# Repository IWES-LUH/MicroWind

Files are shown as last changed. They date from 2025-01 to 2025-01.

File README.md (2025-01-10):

# MicroWind
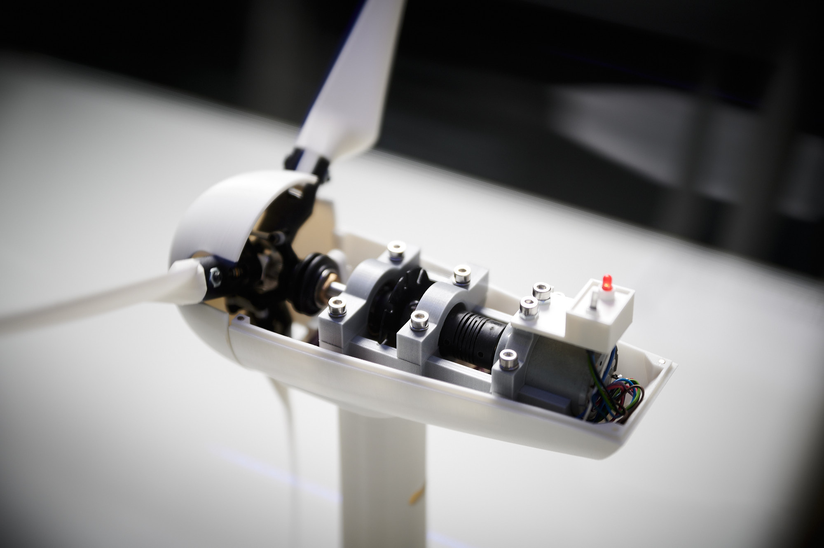
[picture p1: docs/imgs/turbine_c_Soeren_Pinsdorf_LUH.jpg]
Turbine image

*(c) Soeren Pinsdorf / LUH*

MicroWind is an easy to build, 3D-printed miniature wind turbine model 
equipped with various functionalities and sensors. 
The project also features a graphical interface for turbine and wind tunnel control 
and real-time measurement data plots. Its aim is an educational purpose: 
to convey the behavior of a wind turbine in different operation conditions.  
**It is not suited for electricity generation.**  
The repository contains the stl files for 3D printing, the source code for the arduino microcontroller, 
the source code for the graphical interface written in python and tkinter and the documentation.

## Features
* Wind turbine with rotor diameter of 320mm.
* Rated wind speed between 2.5 and 3 m/s.
* Variable blade pitch.
* Variable torque (with limitations).
* Rotation speed measurement.
* Power measurement.
* Thrust force measurement.
* Wind speed measurement with thermal anemometer.
* Bearing friction compensation.
* Compact and appealing wind tunnel design.
* Wind tunnel speeds up to 6 m/s.
* Easy to use user interface for control and measurement display.
* Python template script for easy programming pitch and torque controller (e.g. PID).
* Arcade style game where you have to set pitch in varying wind conditions

## Requirements
The software will be provided as source code to run in a Python interpreter. 
You will need a Python installation and some additional packages to run the software.
Check [requirements.txt](interface/requirements.txt) for the additional packages and 
the installation guideline in the [documentation.md](docs/documentation.md).

The gui works well on Windows systems and is designed and tested on Windows. 
It also works on linux systems with a few minor graphical issues which may be fixed in the future.
The additional package python3-tk is required on debian and python3-tkinter on fedora systems. 
For the arcade game to work properly, a 1920x1200 screen is required. 
For now, the arcade game graphics are not scalable. 

## Required skills
The project is designed for an easy build. However, depending on where and when you are building the turbine, 
some parts may not be available and some alterations must be made. 
Therefore, the project requires some skills:
* Soldering, and basic understanding of electronic circuit design.
* Precise 3D-printing. FDM is fine, but you will need a nozzle size of 0.25 for some parts.
* Postprocessing 3D-printed parts, drilling, inserting threaded inserts.
* Arduino programming, if one of the sensors has to be replaced with a different brand.
* Python programing if you want to tailor the GUI to your needs.
* General troubleshooting ability and patience. 
Even a good documentation is never perfect.  
And this one is not a step by step manual (yet). You may need to dig a little to get it working.  

If you find yourself comfortable tackling the aforementioned requirements then we wish you a **happy build!** 
If you run into trouble don't hesitate to ask.

## Contribution
We decided to publish the project on GitHub, so it is easy for you to contribute. 
Whether you are a software developer willing to improve the code, 
or you stumbled across some shortcomings in the documentation while building, 
we kindly ask you to contribute your upgrades to the project. 
The project is mostly created by mechanical / wind energy engineers, who are not professionals in all fields. 
We believe that there are still many improvements to make. See [contribution.md](contribution.md) for open issues.

## Acknowledgements
The initial MicroWind project was funded for the improvement of study
conditions by the Leibniz University Hannover.

## License
The software is licensed under GPLv3.  
The 3D-parts for printing and the documentation is licensed under CC-BY 4.0.
See [LICENSE.md](LICENSE.md) for more information about GPLv3 and CC-BY 4.0.  

The theme for the GUI is licensed under the MIT license
See [LICENSE-Third-Party.md](LICENSE-Third-Party.md) for more information

## Impressions
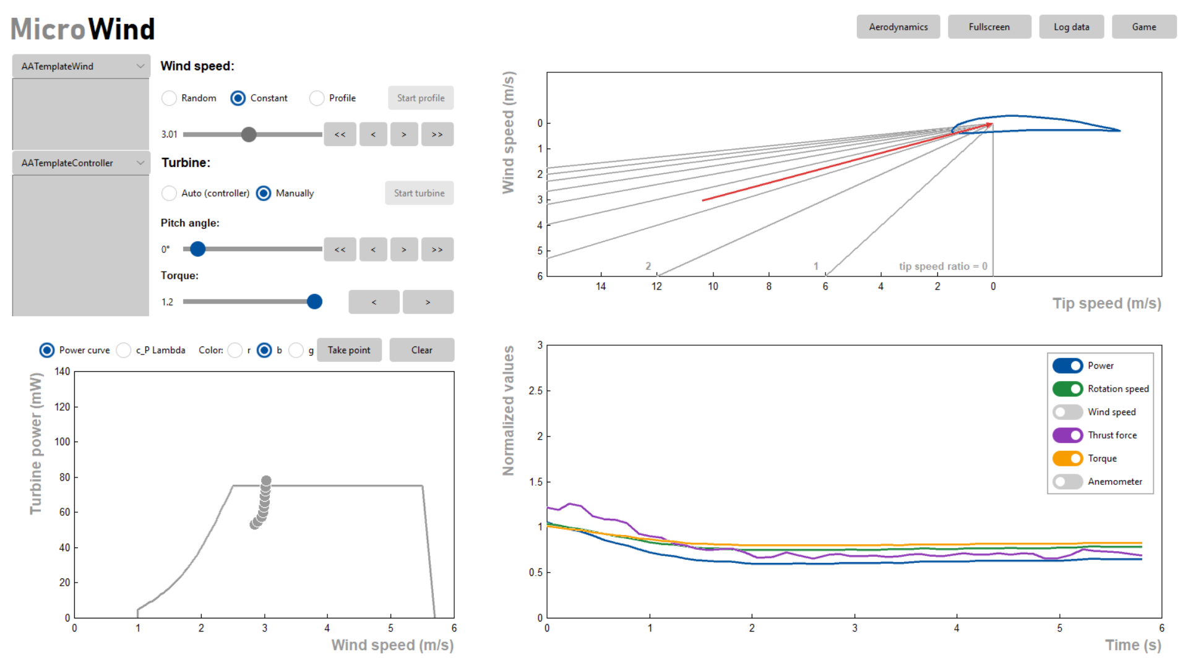
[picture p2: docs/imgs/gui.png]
GUI

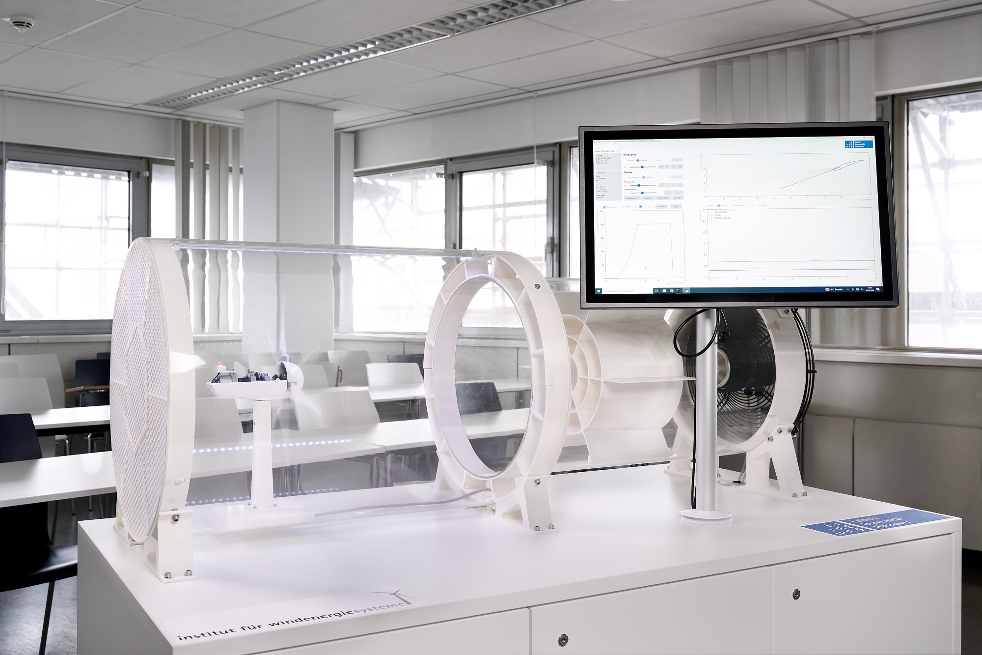
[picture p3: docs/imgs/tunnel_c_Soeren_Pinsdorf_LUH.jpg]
Wind tunnel image

*(c) Soeren Pinsdorf / LUH*

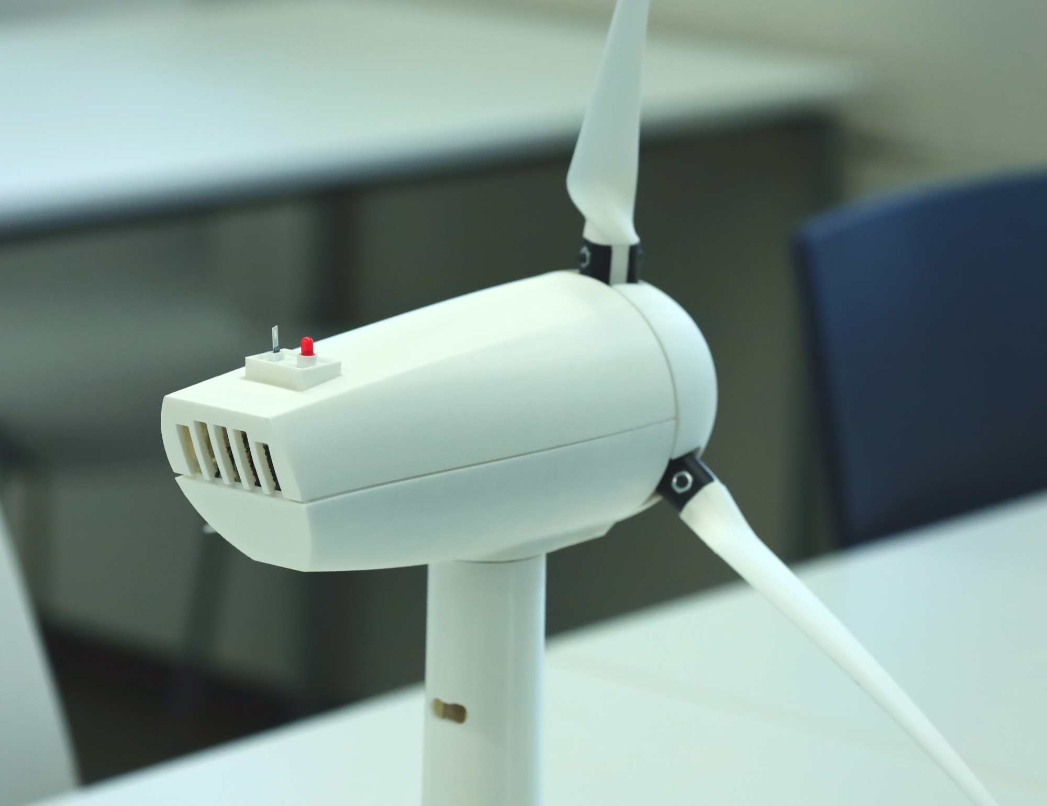
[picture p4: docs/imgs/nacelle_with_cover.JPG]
Nacelle cover


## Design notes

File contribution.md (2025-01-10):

# Contribution
**There is always room for improvements!**  
If you want to be part of the MicroWind project 
feel free to share your valuable knowledge and skills.  
Following a list of things that could be beneficial 
to the project and the building experience:
* Taking pictures of the build process for the documentation. (easy)
* Redesign of tower for easier assembly. (some 3D design experience needed)
* Tolerance tolerant design of all parts that are mounted inside the wind tunnel tubes. (some 3D design experience needed)
* Replace the load resistor switch circuit with 
continuous current control for smooth torque control (electronic skills needed)
* Improve the current measurement, which is very noisy (maybe higher shunt resistor)(electronic skills needed)
* Check if the BS 170 Mosfets can be replaced with IRLD 024, to reduce variety of parts
* Improve the thermal anemometer reading, which is very noisy (electronic skills needed)
* ...

# Contributors
Following a list of contributors to the project:
### 3D-parts design
Louis Mantwill IWES LUH  
Tristan Unnasch IWES LUH  
Marcel Hayduk IWES LUH  
Felix Prigge IWES LUH 
### Circuit design
Felix Prigge IWES LUH  
### Software 
Mohammadsadegh Saei Esfahani IWES LUH  
Felix Prigge IWES LUH  
### Documentation
Felix Prigge IWES LUH

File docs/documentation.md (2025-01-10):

# Documentation

## Challenges of MicroWind
Let's first talk about the difficulties of designing this wind turbine and the wind tunnel. 
This will help to understand the one or the other important steps in the build process.

### Rotor design
First, the turbine operates at is very low wind speeds.
The aim was to design a wind tunnel, 
that is portable between different locations, lecture rooms, exhibitions. 
To achieve this small size, an open wind tunnel was the only possible solution.
An open wind tunnel moves a lot of air and makes noise, which you don't want in public. 
So the design is a compromise of keeping wind speeds as low as possible, 
while allowing the turbine to operate in all modes (idle, partial load, full load, cut-out) 
and clearly distinct between them. 
Wind speeds below 3 m/s are quite difficult to measure precisely without very expensive equipment.
This means calibration of the absolute wind speed is maybe a bit off, 
which affects power coefficient and other values.
But it is actually not as bad as it sounds. 
The main idea behind this project is to show wind turbine operation and not to prove the aerodynamic design.
And this is done by comparing relative values, by the change in rotation speed, 
by the change in power related to different pitch angles. 
And this works great!

Because of the relatively small wind speed and the turbine size, 
we operate in very, very low Reynolds numbers (1000 to 4000).
So don't expect the same aerodynamic performance you would get from a real-sized turbine.
The rotor blades are designed with QBlade and tailored for small Reynolds numbers. 
The tailoring results in very thin and high camber airfoil shapes, 
completely different to the shapes large turbines use. 
We used NACA 9702 at the blade root and NACA 9707 at the blade tip with a constant thickness of the blade, 
which is the minimum required thickness for printing.
A sharp leading edge is quite important to increase performance in these operating conditions.
Thus, a fine nozzle is required for printing the blades.
The rotor design for QBlade v0.963 is provided in the docs folder. 
Figure 1 shows the rotor performance by design. 
With our turbine and wind tunnel, we found a maximum power coefficient of around 0.1 instead of the proposed 0.14. 
This can have multiple reasons. 
Because of the cubic relationship between power and wind speed, 
small errors in wind speed result in large errors in power and power coefficient. 
The wind field in the tunnel is far away from perfect and not adequately filtered. 
Turbulence from the fan and a radially varying wind speed result also has an influence of the aerodynamic performance.
And finally, the assumptions made in the design process of the blades may not correct or precise for such small rotor geometries.
Therefore, we are actually quite happy with the result of the rotor performance given these circumstances. 
However, if you have a very well calibrated wind tunnel with perfect air flow you may encounter better values.

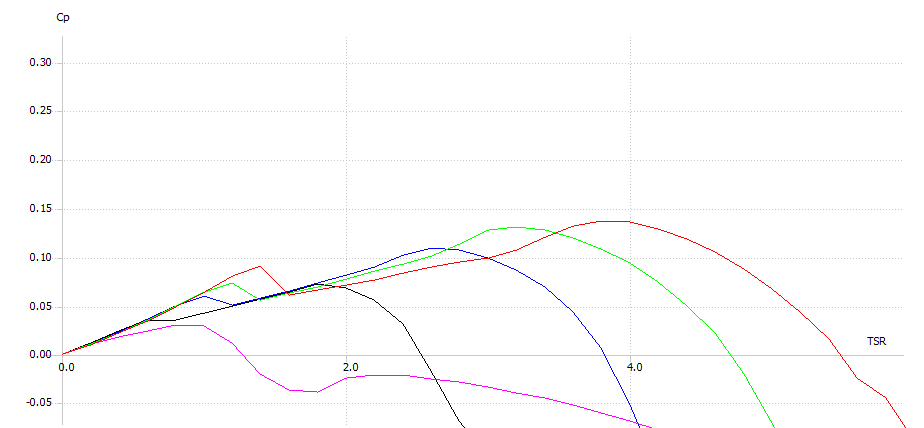
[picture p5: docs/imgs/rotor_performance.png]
Rotor performance
  
_Figure 1: Rotor performance calculated in QBlade for pitch angles of 
0° (red), 5° (green), 10° (blue), 20° (black) and 40° (pink)._

### Wind tunnel design
For the wind tunnel itself, the capability to filter the air flow is limited, 
due to the short design.
It is most important to remove the tangential induction from the fan, 
as this would result in a rotation of the air inside the tube. 
Also, the stream velocity from the fan increases with the radius. 
The filter design tries to compensate this a little 
and increase the velocity in the center of the wind tunnel. 
No doubt, this is not a perfect filtering, but it works surprisingly good.
Feel free to improve it, if you like.

A second problem resulting from the wind tunnel design 
is the short distance between the rotor blade tip and the wall of the wind tunnel. 
To ensure a free stream around the turbine, just like the stream around a real turbine,
we would need to increase the diameter of the tunnel to a size, where you won't get it through a door.  
If the wind tunnel walls are too close, static pressure builds up in the tunnel in front of the turbine,
because the turbine blocks the air flow.
Something that would increase the performance of our little turbine drastically, 
but is not physically correct if we want our turbine to behave like a real one. 
So we must prevent static pressure building up by opening the wind tunnel walls in front of the turbine. 
In our design, this is done by using two different sized tubes: 
a smaller diameter for the fan and a larger diameter for the "test section" where the turbine is located. 
The tubes overlap a little but air can get in and out freely. 
And it does! 
If the turbine is idling and not blocking the stream, 
air gets sucked in the gap between the two tubes by the main air stream. 
As soon as the turbine spins fast and blocks the stream, air gets blown out the gap.
Feel free to experiment with wind tunnel design yourself. 
Depending on your specific needs and what you want to do with the turbine, 
you may come up with a better solution.
If you don't need an outer tube at all, even better for the air stream!

### Generator torque control
Another drawback, which comes from the overall small design, is low torque. 
Physics does not mean it well with small turbines.
Rotor torque increases by the power of two with wind speed 
and by the power of three with rotor radius. 
In addition, the turbine is designed to run at high tip speed ratio, just like real turbines do.
This reduces torque by design in favor of rotation speed for increased aerodynamic efficiency. 
The torque is actually so low, that the remaining friction in the drivetrain has a huge impact.
While real wind turbines have a high mechanical efficiency in the drivetrain 
and low frictional losses in the bearings and the gearbox 
our little turbine has high losses. 
Even though we try to minimize friction by using unsealed and de-greased bearings, 
the electric efficiency may even be below zero, depending on the operation point. 
This is where friction compensation comes into play. 
Depending on the operation point, the generator either works as a motor or generator. 
A small voltage is applied to the generator which creates a moment to compensate the friction.
The frictional loss is then added to the electrical power of the generator, 
which itself can be positive (generator) or negative (motor). 
Thus, **the output we present is not the pure electrical power of the turbine**, 
but the aerodynamic power or drivetrain power. 
Depending on your bearings or your generator,
frictional torque may vary between each build of the turbine. 
So we use a potentiometer to control the necessary current flow for the compensation, 
which can be set individually for each build. 
Measuring this current enables us to determine the frictional torque 
with help of the generator torque constant.

Speaking of the generator torque constant: 
This is a very important parameter not only for determining the frictional loss, 
but the overall electrical power.
At the same time it is not provided by the manufacturer, 
so we tried our best to measure it with a miniature motor-generator test stand. 
It is maybe not very precise, but it as stated in the beginning, 
the main goal of the turbine is to show relative values and not absolute.

Our generator has a linear relationship with just an ohmic load resistor.
However, wind turbines require a quadratic torque vs rotation speed curve, 
to operate efficiently in partial load. 
To be able to model different torque curves, we can switch between different load resistors.
There are six switches with load resistors from 0 ohm to 33 ohm. 
Only one switch is on at a time setting the torque level.
Closing all switches results in a seventh torque level, 
which is ideally torque free for all rotation speeds.

To enable a finer stepping than just seven torque curves, 
we use six additional non-physical torque levels in between by toggling between two physical levels.
The resulting generator curves are shown in Figure 2. 

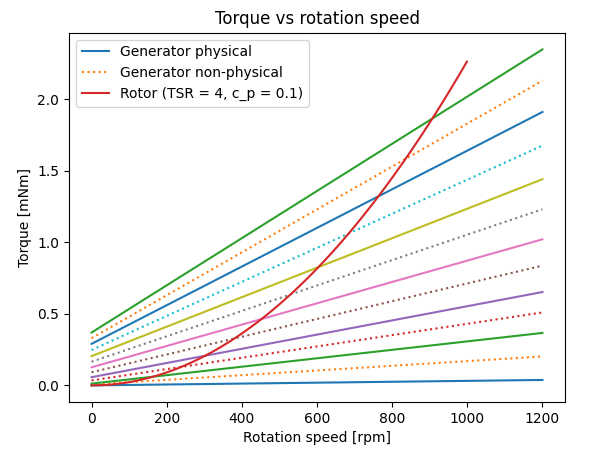
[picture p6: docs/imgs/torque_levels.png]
Torque levels

_Figure 2: Torque vs rotation speed curves for different load switch states. 
The dashed lines are non-physical states by toggling between the upper and lower physical states._

## 3D-Printing Parts
Printing the parts is straight forward. 
The parts are designed to require only a minimum of support structure while printing. 
This way it should be possible to print everything with a single nozzle printer.
It is recommended to use a fine nozzle size (0.25mm) 
for the nacelle's parts to get a nice appearance and a good fit. 
The rotor blades are required to be very thin for optimal aerodynamic performance. 
A 0.25mm nozzle and a high print quality is required here.
The safety grid at the wind tunnel's exit also requires thin walls. 
Otherwise, a fair amount of wind speed is blocked. 
Consider to exclude it if not needed in your application. 
There is not a high potential of danger from the spinning turbine, 
but grabbing inside the tunnel and touching the turbine could lead to damage.  
The large parts of the wind tunnel assembly can be printed with a 0.8mm nozzle. 
One of the challenges you may face is getting the tolerances of the 3D-printed assemblies inside the wind tunnel 
and the tubes for the tunnel right. 
Maybe these parts need a lot of refinishing. 

## Wiring the Sensors
Follow the schematic in [circuit.svg](circuit.svg) to solder the sensors and the additional electronic parts. 
Consider using a large veroboard and place the arduino in the middle. No SMD soldering required.
You are free to choose what kind of cable you use between the turbine and the micro controler. 
This depends on the distance between these two and if it has to be plugable or not. A 15-Pin D-Sub cable could do the job. 

**Be careful:** The resistance of the wires between the generator and the load resistor switch circuit will add up to the generator load.
An increase in the load will decrease the torque vs speed curves of the turbine. 
Possibly, the generator is not able to produce enough torque to reach rated power at rated wind speed. 
Follow the instructions in the schematic to measure the total resitance. 
If your measured resistance is lower, consider adding a resistor to compensate. 
If your resistance is too high, reduce cable length or choose a different cable.

## Assembly
*Ideally, here should follow a lot of images from the build process. Sadly, when we build the first and so far only turbine, 
we didn't consider publishing the project as open source and didn't take any image. 
If you are the first one to build by this instruction, please ask us when in doubt. 
And we would highly appreciate, if you could take some pictures of the build process and share it.*

A few notes:
* Carefully replace the bearings in the pitch slider with cleaned and unsealed ones to reduce friction. 
Probably it is held together with Locktite and difficult to unscrew, but worth the process. 
When putting back together don't tighten too much. The bearings should spin freely.
* Use a tiny bit of Locktite for all the small screws in the pitch assembly, or it will fall apart eventually. 
* You maybe want to run the software with all sensors wired so and set the pitch angle to 40 degrees. 
Then, put the pitch lever on the servo and assemble the rest. This way you already have a rough servo calibration, 
which will speed up the calibration process later.
* The load cell gets damaged really quick, so be careful. Don't apply high loads or torque at the nacelle after the load cell is mounted.
* Place the fan exactly at the center of the tube. Make sure that there is an equal distance between fan blade tips and the wall.

There is one thing quite crucial about the assembly of the nacelle, 
which is the position of the hub relative to the first main bearing. 
We use the main bearing as an end stop to calibrate the pitch angle to 85°, 
thus, a wrong distance will result in a error in pitch angle calibration.
Moreover, if the distance is too large the pitch mechanism can get stuck.
Luckily, the other end stop of the pitch slider is the hub itself. 
So at least for the calibration of the 0° position, 
we are good as long as the printed pitch bones have the correct length. 

The space between the main bearing and the back side of the hub should be 35 mm.
Because this distance is difficult to measure during assembly, we recommend mounting the main shaft with
a distance between the main bearing and the tip of the main shaft of 53.5 mm.
Then the distance between the front side of the hub and the tip of the main shaft should be 7.5mm. 
The assembly is shown in Figure 3.

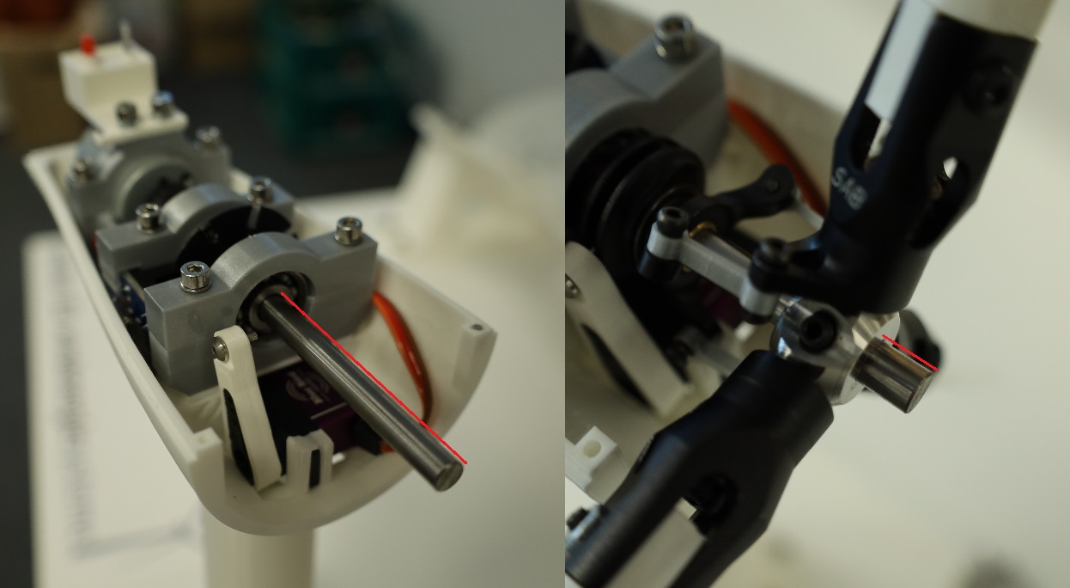
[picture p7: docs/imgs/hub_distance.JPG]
hub distance


_Figure 3: Distances to measure during assembly. Bearing to tip: 53.5 mm. Hub to tip 7.5mm._

## Installation and Running the Interface
1. Flash the [arduino code](../arduino/arduino.ino) to the Arduino Mega using the Arduino IDE.
2. Install the latest Python version on your computer
3. Install the required python packages listed in [requirements.txt](../interface/requirements.txt) using pip installer   

    py -m pip intall requirements.txt

4. Execute the [main.py](../interface/main.py) within Python to start the graphical user interface

    py interface/main.py  

## Command line interface
If you want to control the turbine via command line instead of using the GUI 
you can do so by importing and initializing the Driver class from [driver.py](../interface/driver.py)
Here you can manipulate all the variables and turbine parameters yourself, 
but you have to send and receive the data to and from the arduino manually. 
Here is an example to change the pitch angle to 10 degrees and reading the rotation speed using the command line.

    from interface.modules.driver import Driver
    # Initialize class to control turbine
    turbine = Driver()  
    # retrieve data first
    turbine.read_from_arduino()  
    # change pitch angle variable to 10 degrees
    turbine.beta_set = 10  
    # send data
    turbine.write_to_arduino()  
    # retrieve data
    turbine.read_from_arduino()
    # print rotation speed
    print(turbine.rot_turb)

There is also a command to print all parameters at once.  

    turbine.print_values()

**Warning: There won't be any over speed protection when using the command line interface. 
Speeds above 1200 rpm may damage the turbine, so use this tool with caution.**

## Calibration
### 1. Friction Compensation
As stated in the [challenges section](#Challenges-of-MicroWind), 
we compensate the friction of the drivetrain by applying a small voltage to the generator.
To calibrate the amount of compensation use the 200 ohm potentiometer shown in the [circuit.svg](circuit.svg).
Do so while the power supply is on and the arduino is connected via USB. 
But do not start the interface. This ensures that all load resistors are switched off. 
Set the potentiometer so that the turbine does not start spinning on its own. 
Give the rotor a little push, the rotor should continue to spin at very, very low speed and not stop.

### 2. Pitch Angle Calibration
To calibrate the pitch angle it is best to remove the upper cover of the nacelle and the spinner.
Run the calibration script [calibrate_pitch.py](../interface/calibrate_pitch.py) 

    py interface/calibrate_pitch.py

and incrementally add or remove servo time until the pitch slider touches the physical limits.
If assembled correctly, this will result in a pitch range of -5° to 85°.

### 3. Thrust Force Calibration 
To calibrate the thrust force, you will need some kind of spring force gauge or be creative.
Run the calibration script [calibrate_thrust.py](../interface/calibrate_thrust.py) 

    py interface/calibrate_thrust.py

and follow the instructions.

### 3. Wind Tunnel Calibration
Next the wind speed of the tunnel will be calibrated. 
We do this by the assumption that the turbine is spinning with a tip speed ratio of 2.5 at a pitch angle of 20 degrees.
Run the calibration script [calibrate_wind.py](../interface/calibrate_wind.py) 

    py interface/calibrate_wind.py

and follow the instructions.

### 4. Torque Calibration
Once the pitch and wind speed is calibrated, 
we can run the torque calibration [calibrate_wind.py](../interface/calibrate_wind.py):

    py interface/calibrate_torque.py

### 5. Thermal Anemometer Calibration
Now that the wind speeds are calibrated, we can calibrate the thermal anemometer.
Run the calibration script [calibrate_anemometer.py](../interface/calibrate_anemometer.py) :

    py interface/calibrate_anemometer.py

Maybe the range of the anemometer is not set right 
and the output is saturated either at the lower or the upper end.
In this case try to tune the amplification of the anemometer with the potentiometer and try again.

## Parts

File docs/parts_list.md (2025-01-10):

## Electronics:
* 12V Power supply
* 7805 TO-220 Voltage regulator
* Arduino Mega 2560
* Load cell: TAL221, 100g
* Load cell board HX711
* Generator: Euklit RF-370CHV-22170 
* Current sensor: INA219 
* Mini IR speed sensor (https://www.androegg.de/shop/mini-ir-geschwindigkeits-speed-sensor/)
* Servo: Blue Bird Servo BMS-210DMH
* Generator load switch circuit:
	* 6x IRLD 024 N-Channel Mosfet RDS(on) 0.1 Ohm
	* Resistor 3.3 Ohm 3W (For a cable resistance between generator and load of 3.5 Ohm) 
	* Resistor 6.8 Ohm 3W
	* Resistor 15 Ohm 3W
	* Resistor 33 Ohm 3W
	* 2x Resistor 100 Ohm 3W
    * 330nF elko
* Thermal anemometer: 
	* FLW-122
	* LM2902
	* BC 635 NPN Transistor
	* 500 Ohm trim potentiometer
* Pitch Potentiometer: 5k linear
* 3mm LED Red 2mA
* Additional resistors, transistors and elkos see schematic
* Veroboard or couple arduino prototyping shieds (Would use a large veroboard next time)
* Switching wires
* Connecting cable to turbine (D-Sub 15pin for example)

# Tunnel:
* Systemair AW 350 EC sileo
* Connecting cable to fan (D-Sub 9pin for example)
* (Acrylic glass) tube D=400, d=392, l = 700
* (Acrylic glass) tube D=500, d=492, l = 700
* Screws:
	* 24x ISO 4762 M6x16 (mounting on desk)
	* 24x M6 insert (mounting on desk)
	* 2x ISO 4762 M6x50 (fan assembly top)
	* 2x ISO 4762 M6x70 (fan assembly bottom)
	* 8x ISO 4762 M6x16 (inner tube)
	* 4x ISO 4762 M6x14 (outer tube)
	* 2x ISO 7046 M6x12 (outer tube)
	* M6 threaded insert for 3D printed parts
  
# Turbine Hardware:
* Pitch mechanics: Sab Goblin 630/700/770 3-Blade Tail Unit
* 2x Replacement bearings for pitch mechanics: SS MF128 W2.5 8x12x2.5 (stainless, unsealed, delubricated for low friction) 
* Main shaft: D=6mm h6, 95mm length
* 2x Main bearings: SS MR126 W3 6x12x3 mm (stainless, unsealed, delubricated for low friction) 
* 2x Adjusting ring d=6mm (could also be 3D printed)
* Generator coupling: skps 1520 02/06 (remove (saw) one of each pair of bars to incease flexibility)(3D printed claw coupling could also work) 
* Screws:
	* 5x ISO 7380 M3x16 (3x blades, 2x load cell) 
	* 2x ISO 7380 M3x12 (load cell) 
	* 4x ISO 4762 M3x25 (main bearing assembly)
    * 2x ISO 4762 M3x14 (motor assembly)
	* 2x ISO 4762 M3x6  (led and anemometer deck assembly)
	* 8x ISO 4762 M3x10 (tower assembly)
	* M3 threaded insert for 3D printed parts (short version for deck assembly)
	* M3 washers
	* M3 hex nuts

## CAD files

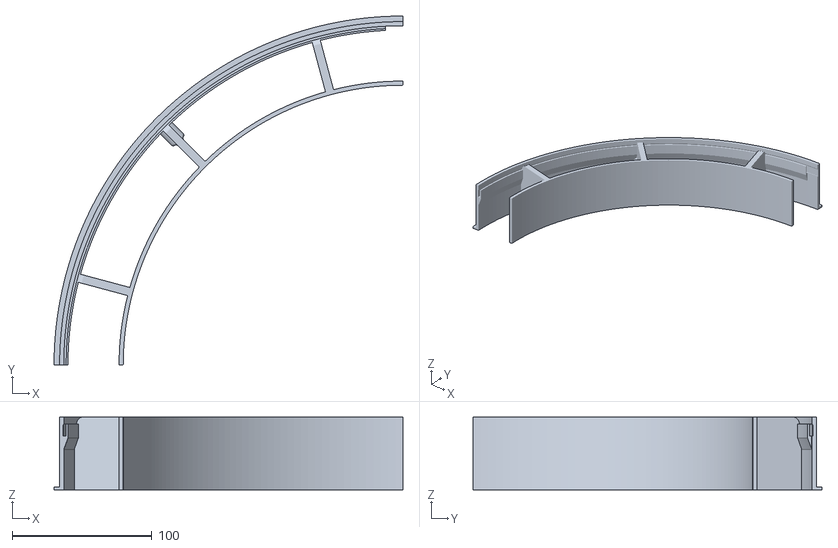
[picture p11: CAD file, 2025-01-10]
3D_print/Tunnel/tube_intermediate.stl
249.5 x 249.5 x 52.0

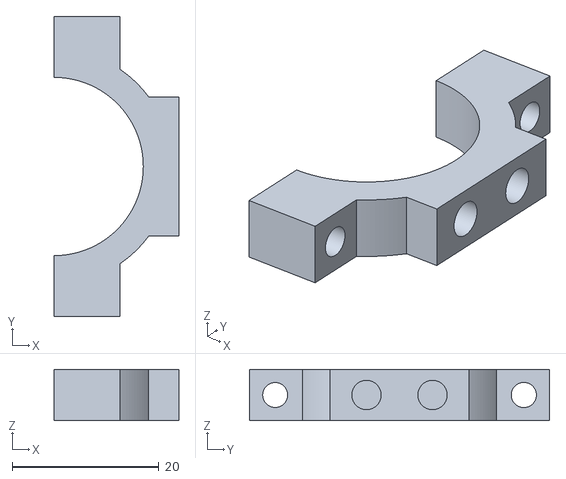
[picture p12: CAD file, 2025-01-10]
3D_print/Turbine/generator_bracket.stl
17.0 x 40.9 x 7.00

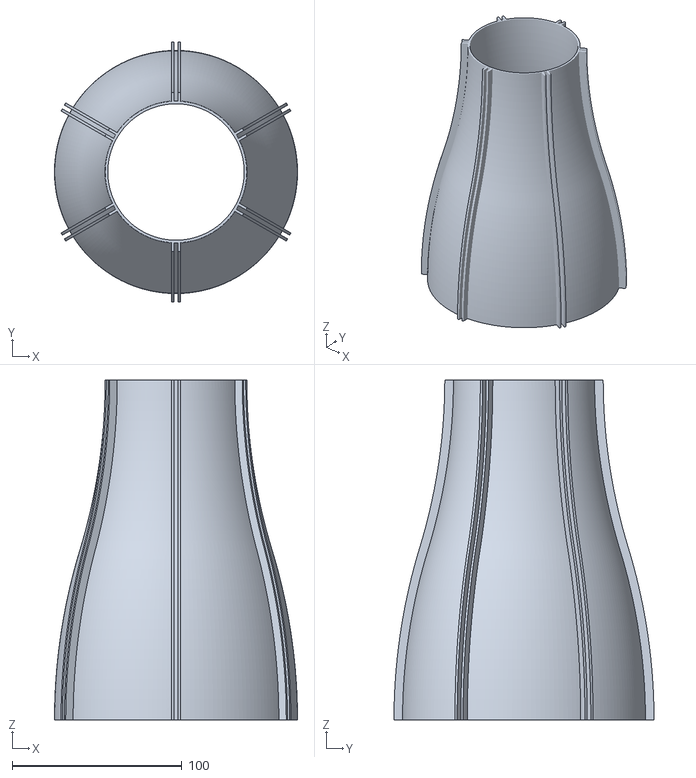
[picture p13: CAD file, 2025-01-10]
3D_print/Tunnel/diffusor_b.stl
143.0 x 153.0 x 200.0

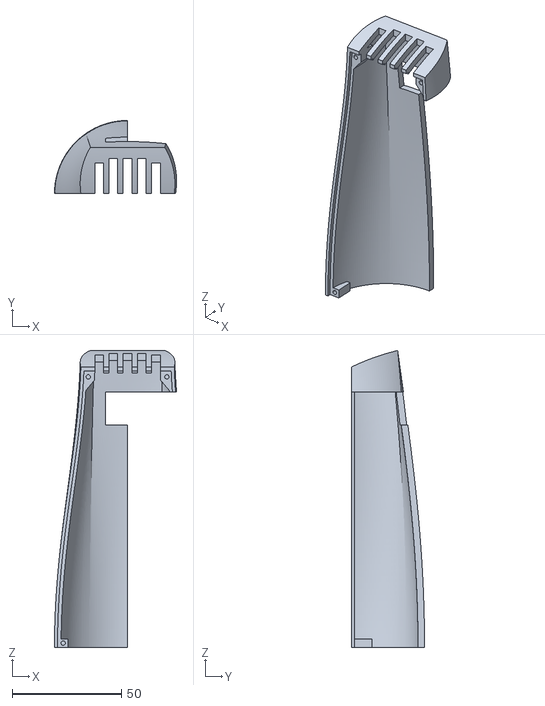
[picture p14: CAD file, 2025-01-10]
3D_print/Turbine/nacelle_top_open.stl
56.0 x 33.5 x 136.1

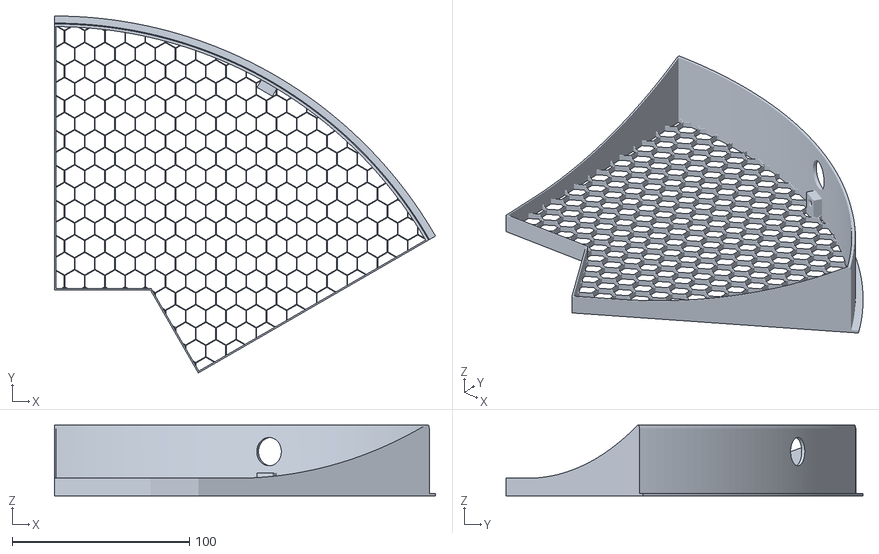
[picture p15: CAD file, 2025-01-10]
3D_print/Tunnel/safety_b.stl
215.2 x 201.6 x 40.0

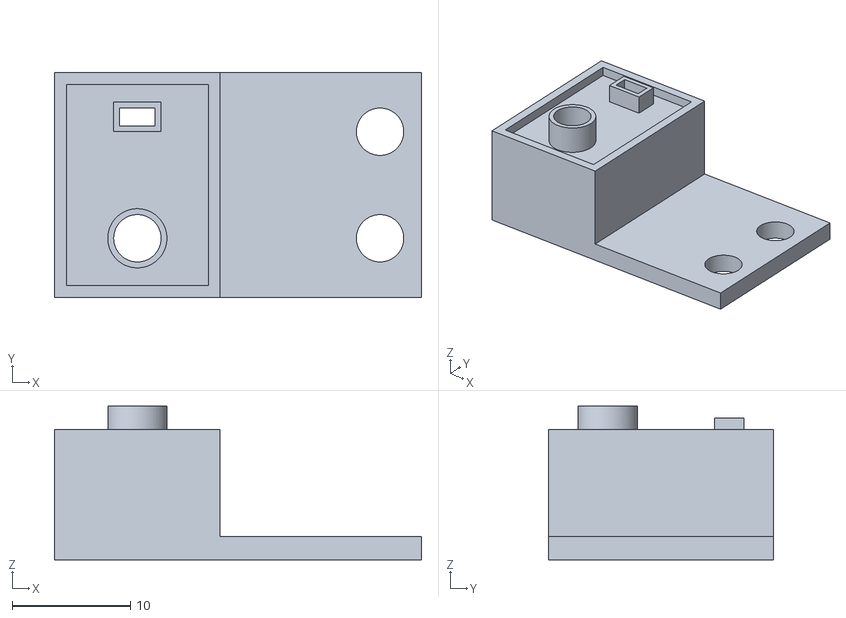
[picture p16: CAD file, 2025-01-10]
3D_print/Turbine/deck.stl
31.0 x 19.0 x 13.0

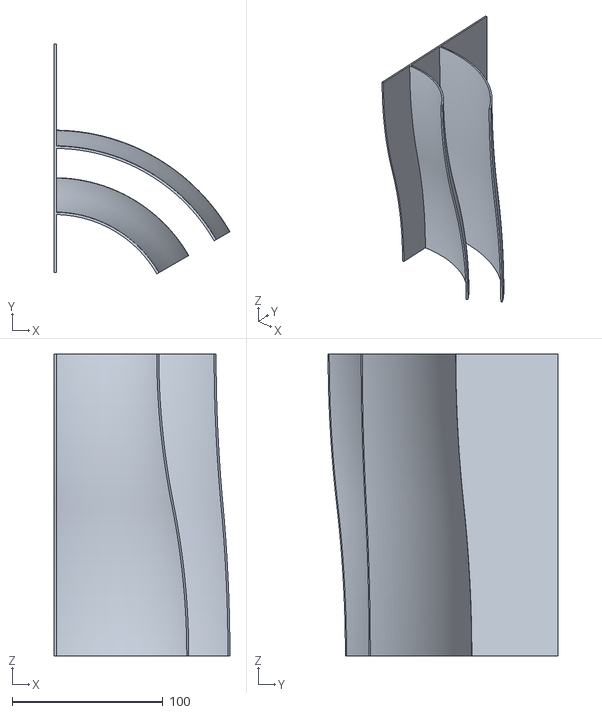
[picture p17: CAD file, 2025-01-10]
3D_print/Tunnel/diffusor_a.stl
116.5 x 152.2 x 200.0

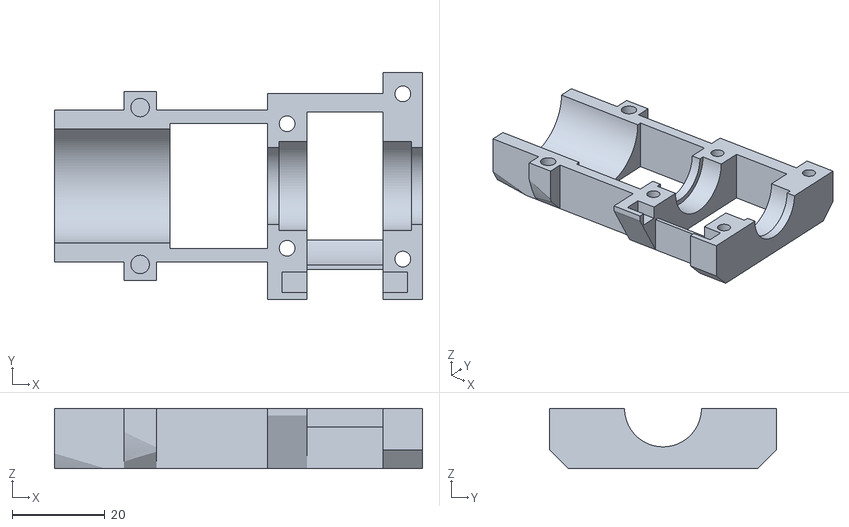
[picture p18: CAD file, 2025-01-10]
3D_print/Turbine/nacelle_inner.stl
79.5 x 49.0 x 13.0

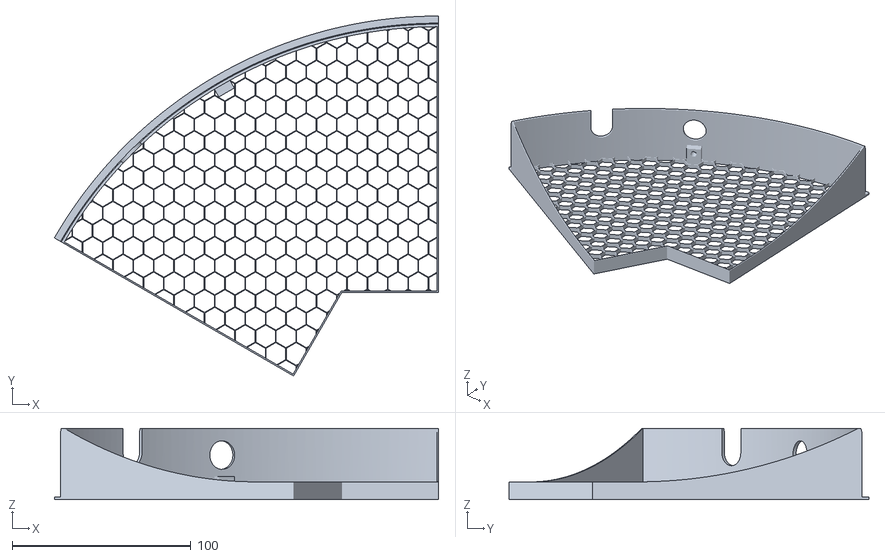
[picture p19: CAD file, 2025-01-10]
3D_print/Tunnel/safety_c_mirror.stl
215.2 x 201.6 x 40.0

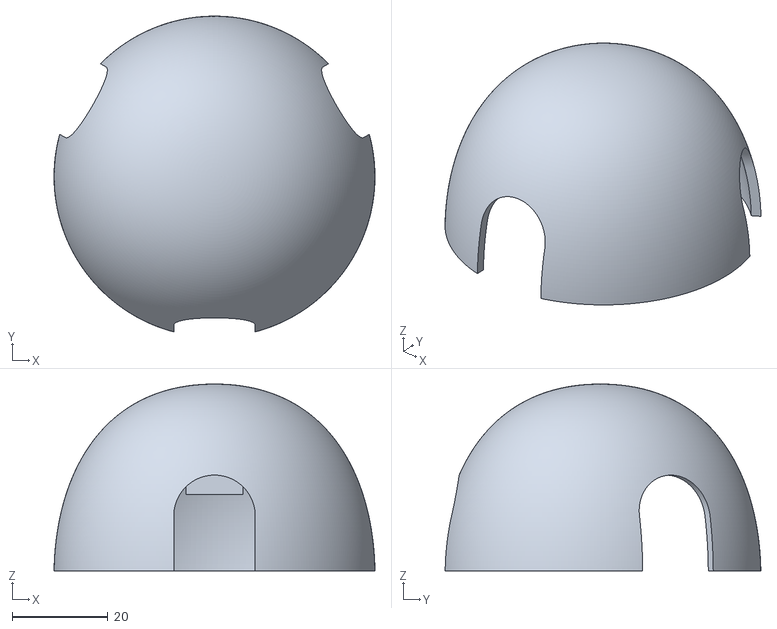
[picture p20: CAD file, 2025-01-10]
3D_print/Turbine/spinner.stl
67.0 x 65.9 x 39.0

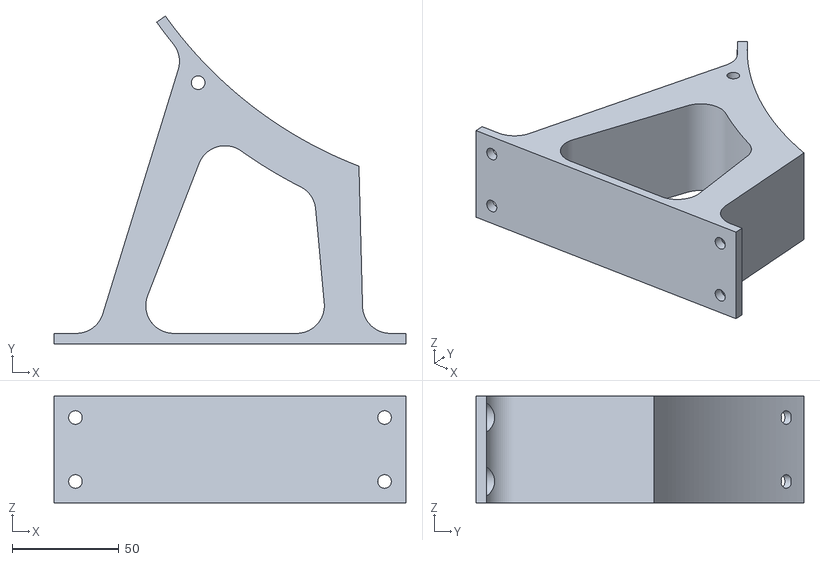
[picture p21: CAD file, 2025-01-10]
3D_print/Tunnel/inner_tube_base.stl
165.0 x 153.9 x 50.0

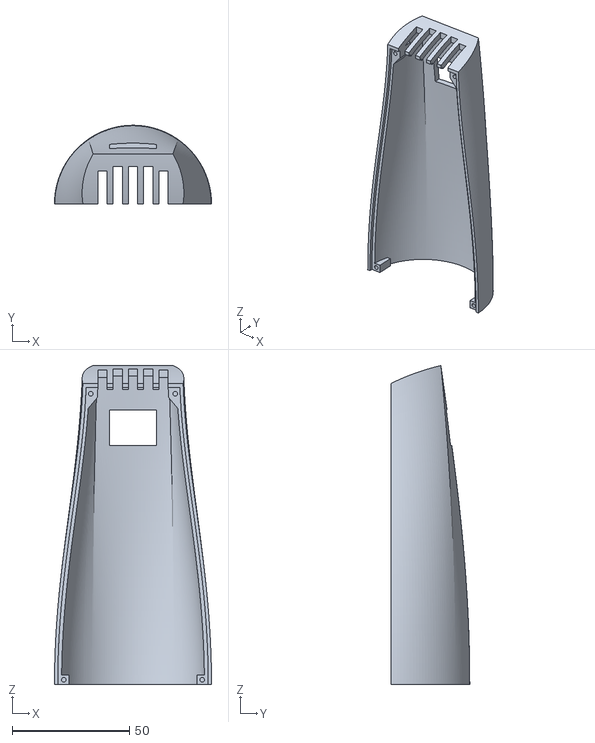
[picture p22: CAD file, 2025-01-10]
3D_print/Turbine/nacelle_top.stl
67.0 x 33.5 x 136.1

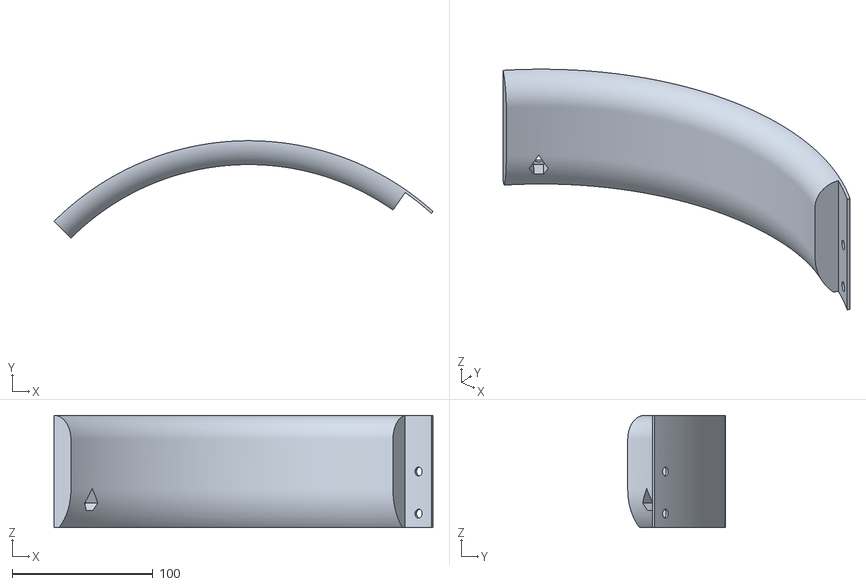
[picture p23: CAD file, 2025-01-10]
3D_print/Tunnel/fan_ring_side_mirror.stl
269.7 x 69.4 x 80.0

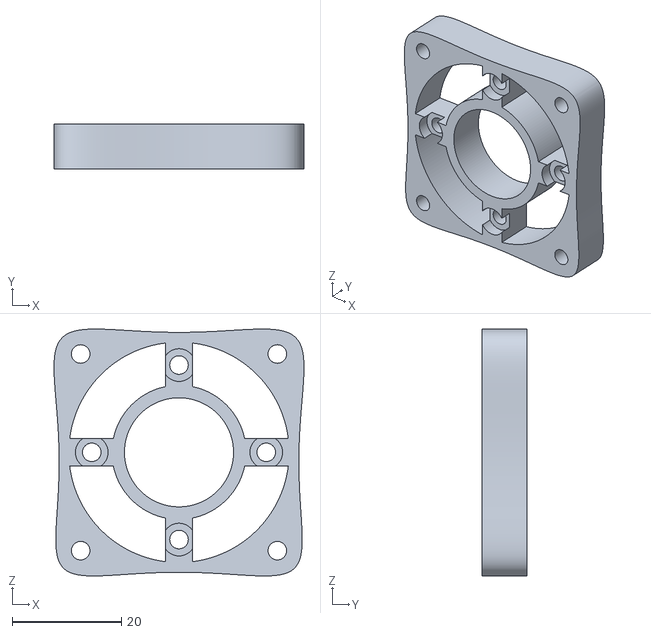
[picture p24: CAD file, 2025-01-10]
3D_print/Turbine/tower_base.stl
45.8 x 8.20 x 45.3

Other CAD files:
3D_print/Tunnel/safety_spring.stl
3D_print/Turbine/nacelle_bottom.stl
3D_print/Tunnel/fan_ring_bottom.stl
3D_print/Turbine/pitch_bone.stl
3D_print/Tunnel/diffusor_base.stl
3D_print/Tunnel/fan_mount_top.stl
3D_print/Tunnel/fan_ring_side.stl
3D_print/Tunnel/fan_ring_top.stl
3D_print/Tunnel/inventor/diffusor_a.ipt
3D_print/Tunnel/inventor/diffusor_b.ipt
3D_print/Tunnel/inventor/diffusor_base.ipt
3D_print/Tunnel/inventor/fan_mount_top.ipt
3D_print/Tunnel/inventor/fan_ring_bottom.ipt
3D_print/Tunnel/inventor/fan_ring_side.ipt
3D_print/Tunnel/inventor/fan_ring_side_mirror.ipt
3D_print/Tunnel/inventor/fan_ring_top.ipt
3D_print/Tunnel/inventor/inner_tube_base.ipt
3D_print/Tunnel/inventor/outer_tube_base.ipt
3D_print/Tunnel/inventor/safety_a.ipt
3D_print/Tunnel/inventor/safety_b.ipt
3D_print/Tunnel/inventor/safety_c.ipt
3D_print/Tunnel/inventor/safety_c_mirror.ipt
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

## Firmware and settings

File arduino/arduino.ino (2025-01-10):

// This file is part ot the MicroWind project, a wind tunnel and wind turbine model
// Copyright (c) 2024 Institute for Wind Energy Systems, Leibniz University Hannover
// The MicroWind software is licensed under GPLv3
// Authors: Felix Prigge

//LIBRARIES
#include <Wire.h>
#include <INA219_WE.h>
INA219_WE CurrentSensor = INA219_WE(0x40);
#define I2C_ADDRESS
#include <Servo_Hardware_PWM.h>
Servo PitchServo;

// PIN DEFINITION
const int PIN_SERVO               = 2;
const int PIN_TURBINE_TACHO       = 18;
const int PIN_FAN_TACHO           = 19;
const int PIN_FAN_PWM             = 45;
const int PIN_FORCE_CLK           = 8;
const int PIN_FORCE_DATA          = 9;
const int PIN_TORQUE_1            = 22;
const int PIN_TORQUE_2            = 23;
const int PIN_TORQUE_3            = 24;
const int PIN_TORQUE_4            = 25;
const int PIN_TORQUE_5            = 26;
const int PIN_TORQUE_6            = 27;
const int PIN_TORQUE_START        = 30;
const int PIN_LED                 = 13;
const int PIN_ANEMOMETER          = A0;
const int PIN_POTENTIOMETER       = A1;

// VARIABLES
uint8_t fan_pwm                           = 0;
uint16_t us_servo                         = 1500;
volatile unsigned long time_fan_tick      = micros();
volatile unsigned long time_turbine_tick  = micros();
unsigned long dt_fan_mean                 = 0;
unsigned long dt_turbine_mean             = 0;
volatile bool rotating_fan                = false;
volatile bool rotating_turbine            = false;
uint16_t speed_fan                        = 0;
uint16_t speed_turbine                    = 0;
float currentfloat                        = 0;
uint16_t current                          = 0;
float voltagefloat                        = 0;
uint16_t voltage                          = 0;
uint32_t thrust_force                     = 0;
uint32_t thrust_force_offset              = 0;
uint16_t anemometer                       = 0;
uint16_t potentiometer                    = 0;
uint8_t torque_level                      = 0;
uint8_t * torque_level_pointer            = &torque_level;
int torque_toggle                         = 1;
int * torque_toggle_pointer               = &torque_toggle;
uint8_t led                               = 0;

// ROTARY BUFFERS
volatile unsigned long rot_turbine_tick[8];  // 8 values stored for averaging (1/2 revolution)
uint8_t pos_turbine_tick = 0;
volatile unsigned long rot_fan_tick[2];      // 2 values stored for averaging (1 revolutions)
uint8_t pos_fan_tick = 0;

void setup() {
  // put your setup code here, to run once:
  // attach servo
  PitchServo.attach(PIN_SERVO);
  PitchServo.writeMicroseconds(1500);
  Wire.begin();

  // define pin functions
  pinMode(PIN_TURBINE_TACHO, INPUT);
  pinMode(PIN_FAN_TACHO, INPUT_PULLUP);
  pinMode(PIN_FAN_PWM, OUTPUT);
  analogWrite(PIN_FAN_PWM, 0);
  pinMode(PIN_FORCE_CLK, OUTPUT);
  digitalWrite(PIN_FORCE_CLK, LOW);
  pinMode(PIN_FORCE_DATA, INPUT);
  pinMode(PIN_TORQUE_1, OUTPUT);
  digitalWrite(PIN_TORQUE_1, LOW);
  pinMode(PIN_TORQUE_2, OUTPUT);
  digitalWrite(PIN_TORQUE_2, LOW);
  pinMode(PIN_TORQUE_3, OUTPUT);
  digitalWrite(PIN_TORQUE_3, LOW);
  pinMode(PIN_TORQUE_4, OUTPUT);
  digitalWrite(PIN_TORQUE_4, LOW);
  pinMode(PIN_TORQUE_5, OUTPUT);
  digitalWrite(PIN_TORQUE_5, LOW);
  pinMode(PIN_TORQUE_6, OUTPUT);
  digitalWrite(PIN_TORQUE_6, LOW);
  pinMode(PIN_TORQUE_START, OUTPUT);
  digitalWrite(PIN_TORQUE_START, HIGH);
  pinMode(PIN_LED, OUTPUT);
  digitalWrite(PIN_LED, HIGH);
  pinMode(PIN_ANEMOMETER, INPUT);
  pinMode(PIN_POTENTIOMETER, INPUT);
  
  CurrentSensor.init();
  CurrentSensor.setADCMode(BIT_MODE_12);// 12 Bit Resolution
  CurrentSensor.setMeasureMode(CONTINUOUS); // choose mode and uncomment for change of default
  CurrentSensor.setPGain(PG_40);// max 0.4 A
  CurrentSensor.setBusRange(BRNG_16); // max 16V

  delay(10);
  // set gain for force sensor
  hx711_set_gain();
  delay(500);
  thrust_force_offset = hx711_read_force();

  // change the timer 5 prescaler to increase the PWM frequency for the fan. Leave everyting else as is
  TCCR5B = TCCR5B & 0b11111000 | 0x02; //Timer 5 is a 16-Bit timer. Prescaler set to 8. Resulting frequency ~ 8kHz 
  
  // set timer 4 for the torque level toggle interrupt. Thanks to https://dbuezas.github.io/arduino-web-timers
  TCCR4B = (1<<WGM42) | (1<<CS41); // CTC-mode, prescaler = 8
  TIMSK4 = 1<<OCIE4A;
  OCR4A = 10000; // toggle every 5ms (ORC4A*prescaler/16Mhz)

  // attach pin interrupt functions
  attachInterrupt(digitalPinToInterrupt(PIN_TURBINE_TACHO), turbine_interrupt, CHANGE);
  attachInterrupt(digitalPinToInterrupt(PIN_FAN_TACHO), fan_interrupt, CHANGE);

  // begin serial connection
  Serial.begin(38400);
  delay(100);
  digitalWrite(PIN_LED, LOW);  
}

void loop() {
  // put your main code here, to run repeatedly:

  // wait for data request
  while (Serial.available() == 0) {}
  Serial.read();

  // calculate data
  noInterrupts();
  if (rotating_fan == true) {
    if (micros() - time_fan_tick < 500000ul) {
      dt_fan_mean = rot_fan_tick[0];
      dt_fan_mean += rot_fan_tick[1];
      dt_fan_mean /= 2;
      speed_fan = 60000000 / dt_fan_mean / 2; // two ticks per rotation
    }
    else {
      speed_fan = 0;
      rotating_fan = false;
    }
  }
  if (rotating_turbine == true) {
    if (micros() - time_turbine_tick < 625000ul) {
      dt_turbine_mean = rot_turbine_tick[0];
      dt_turbine_mean += rot_turbine_tick[1];
      dt_turbine_mean += rot_turbine_tick[2];
      dt_turbine_mean += rot_turbine_tick[3];
      dt_turbine_mean += rot_turbine_tick[4];
      dt_turbine_mean += rot_turbine_tick[5];
      dt_turbine_mean += rot_turbine_tick[6];
      dt_turbine_mean += rot_turbine_tick[7];
      dt_turbine_mean /= 8;
      speed_turbine = 60000000 / dt_turbine_mean / 16; // 16 ticks per rotation
    }
    else {
      speed_turbine = 0;
      rotating_turbine = false;
    }
  }
  interrupts();
  
  currentfloat = 0.2 * CurrentSensor.getCurrent_mA() + 0.8 * currentfloat;
  current = (uint16_t)currentfloat;
  voltagefloat = CurrentSensor.getBusVoltage_V() * 1000.0;
  voltage = (uint16_t)voltagefloat;
  
  noInterrupts();
  if (digitalRead(PIN_FORCE_DATA) == LOW) {
    thrust_force = hx711_read_force();
  }
  anemometer = analogRead(PIN_ANEMOMETER);
  potentiometer = analogRead(PIN_POTENTIOMETER);
  interrupts();
  
  //write data
  Serial.write((byte*)(&speed_fan), 2); // 2bytes
  Serial.write((byte*)(&speed_turbine), 2); // 2bytes
  Serial.write((byte*)(&current), 2); // 2bytes
  Serial.write((byte*)(&voltage), 2); // 2bytes
  Serial.write((byte*)(&thrust_force), 4); // 4bytes
  Serial.write((byte*)(&anemometer), 2); // 2bytes
  Serial.write((byte*)(&potentiometer), 2); // 2bytes
  
  //read data
  while (Serial.available() == 0) {}
  analogWrite(PIN_FAN_PWM, Serial.read());
  while (Serial.available() == 0) {}
  us_servo = Serial.read();
  while (Serial.available() == 0) {}
  us_servo |= (Serial.read() << 8); // 2 byte little endian
  PitchServo.writeMicroseconds(us_servo);
  while (Serial.available() == 0) {}
  *torque_level_pointer = Serial.read();
  while (Serial.available() == 0) {}
  led = Serial.read();

  digitalWrite(PIN_LED, led); 
}

// Interrupts
ISR(TIMER4_COMPA_vect) {
  torque_level_set();
}

void fan_interrupt() {
  if (micros() - time_fan_tick > 20000ul) {
    rot_fan_tick[pos_fan_tick % 2] = micros() - time_fan_tick;
    time_fan_tick = micros();
    pos_fan_tick++;
    rotating_fan = true;
  }
}

void turbine_interrupt() {
  if (micros() - time_turbine_tick > 1000ul) {
    rot_turbine_tick[pos_turbine_tick % 8] = micros() - time_turbine_tick;
    time_turbine_tick = micros();
    pos_turbine_tick++;
    rotating_turbine = true;
  }
}

// Functions
uint32_t hx711_read_force() {
  uint32_t value = 0;
  uint32_t mask = 0x00800000; // 1 at the 24th bit

  while (mask > 0) {
    digitalWrite(PIN_FORCE_CLK, HIGH);
    delayMicroseconds(1);   // T2  >= 0.2 us
    if (digitalRead(PIN_FORCE_DATA) == HIGH)
    {
      value |= mask;
    }
    digitalWrite(PIN_FORCE_CLK, LOW);
    delayMicroseconds(1);   // keep duty cycle ~50%
    mask >>= 1;
  }
  hx711_set_gain();
  return value - thrust_force_offset;
}

void hx711_set_gain() {
  for (int i = 0; i < 3; i++) { // set gain
    digitalWrite(PIN_FORCE_CLK, HIGH);
    delayMicroseconds(1);   // T2  >= 0.2 us
    digitalWrite(PIN_FORCE_CLK, LOW);
    delayMicroseconds(1);   // keep duty cycle ~50%
  }
}

void torque_level_set() {
  // switch off all pins
  digitalWrite(PIN_TORQUE_START, HIGH);
  digitalWrite(PIN_TORQUE_1, LOW);
  digitalWrite(PIN_TORQUE_2, LOW);
  digitalWrite(PIN_TORQUE_3, LOW);
  digitalWrite(PIN_TORQUE_4, LOW);
  digitalWrite(PIN_TORQUE_5, LOW);
  digitalWrite(PIN_TORQUE_6, LOW);

  // switch on turbine start transistor if turbine start
  if (torque_level == 255){  // aka -1
    digitalWrite(PIN_TORQUE_START, LOW);
    return;
  }

  // from 13 software levels to 7 physical levels
  int t_l;
  if (torque_level % 2 == 0){
    t_l = torque_level/2;
  }
  else{
    // toggle between two levels
    t_l = (torque_level+torque_toggle)/2;
    *torque_toggle_pointer *= -1;        
  }

  // set physical torque levels
  if (t_l == 0){
    // leave all switches turned off
  }
  else if (t_l == 1){
    digitalWrite(PIN_TORQUE_1, HIGH);
  }
  else if (t_l == 2){
    digitalWrite(PIN_TORQUE_2, HIGH);
  }  
  else if (t_l == 3){
    digitalWrite(PIN_TORQUE_3, HIGH);
  }
  else if (t_l == 4){
    digitalWrite(PIN_TORQUE_4, HIGH);
  }
  else if (t_l == 5){
    digitalWrite(PIN_TORQUE_5, HIGH);
  }
  else if (t_l == 6){
    digitalWrite(PIN_TORQUE_6, HIGH);
  }
}

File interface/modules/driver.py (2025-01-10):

"""
This file is part ot the MicroWind software to control and plot data of a wind tunnel including a miniature wind turbine
Copyright (c) 2024 Institute for Wind Energy Systems, Leibniz University Hannover
The MicroWind software is licensed under GPLv3
Authors: Felix Prigge
"""

from math import cos, sin, atan
from scipy.interpolate import interp1d
import numpy as np
import time
import serial
import serial.tools.list_ports
import warnings
import interface.data.calibration_data as cal


class Driver:
    """MicroWind driver class
    Stores all data, performs internal calculations and is responsible for communication with the arduino.
    Can be used as a standalone command line control tool.
    """

    def __init__(self):
        # CONSTANTS
        self.AIR_DENS = 1.225
        self.ROTOR_RADIUS = 0.16
        self.ROTOR_INERTIA = 0.2  # Just a rough guess but seems to be ok
        self.PITCH_IDLE = 45
        self.ROT_MAX = 1200
        self.ROT_RATED = 600
        self.POWER_RATED = 75
        self.WIND_IN = 1
        self.WIND_RATED = 2.5
        self.WIND_OUT_1 = 5.5
        self.WIND_OUT_2 = 5.7
        self.THRUST_RATED = 100
        self.TORQUE_RATED = 1.2
        # Servo time limits
        self.SERVO_T_MIN = 1000  # Standard min pulse for servo
        self.SERVO_T_MAX = 2000  # Standard max pulse for servo
        # Fan PWM limits
        self.FAN_PWM_MIN = 6
        self.FAN_PWM_MAX = 255
        # Min max value of pitch
        self.PITCH_MIN = -5
        self.PITCH_MAX = 85
        # Min max value of wind speed
        self.V_MIN = 0.4
        self.V_MAX = 6
        # Min max value of torque levels
        self.TORQUE_LEVEL_MIN = -1
        self.TORQUE_LEVEL_MAX = 13

        # Input variables
        self.fan_pwm = self.FAN_PWM_MIN  # Protected property. Uses setter method for safety
        self.v_set = self.V_MIN  # Protected property. Uses setter method for safety
        self.servo_time = self.SERVO_T_MIN  # Protected property. Uses setter method for safety
        self.beta_set = self.PITCH_IDLE  # Protected property. Uses setter method for safety
        self.torque_level = 0  # Protected property. Uses setter method for safety
        self.led = True

        # Output variables
        self.time_last = time.time()
        self.dt = 1
        self.dt_rw = 0
        self.dt_r = 0
        self.rot_fan = 0
        self.rot_turb = 0
        self.rot_turb_last = 0
        self.current = 0
        self.voltage = 0
        self.thrust = 0
        self.anemometer = 0
        self.potentiometer = 0
        self.beta_potentiometer = 0
        self.tip_speed = 0
        self.power_turb = 0
        self.power_aero = 0
        self.power_wind = 0
        self.v_1 = 0
        self.v_anem = 0
        self.c_p = 0
        self.c_p_aero = 0
        self.v_2 = 0
        self.v_rot = 0
        self.v_rel = 0
        self.phi = 0
        self.torque = 0
        self.torque_force = 0
        self.res_force = np.asarray([0, 0])
        self.lift_force = np.asarray([0, 0])
        self.drag_force = np.asarray([0, 0])
        self.thrust_force = 0
        self.tip_speed_ratio = 0
        self.print_counter = 0

        # Interpolation for thermal anemometer
        self.interp_anemometer = interp1d(cal.ANEMOMETER_READ, cal.ANEMOMETER_WIND,
                                          kind='quadratic', fill_value='extrapolate')

        # Initialize serial communication to arduino
        self.port = serial.Serial()
        self.arduino_connected = False
        self.data_received = False
        self.torque_flip = 0.5
        self.attach_arduino()

    # Data transfer
    # Initialize serial connection
    def attach_arduino(self):
        arduino_ports = [
            p.device
            for p in serial.tools.list_ports.comports()
            if 'Arduino' in p.description]
        try:
            self.port = serial.Serial(arduino_ports[0], baudrate=38400)
            self.port.flushInput()
            self.port.flushOutput()
            time.sleep(2)
            self.arduino_connected = True
        except:
            warnings.warn('Arduino not connected', TransmissionWarning)

    # Receive data
    def read_from_arduino(self):
        try:
            if not self.data_received:
                self.port.write((1).to_bytes(1, byteorder='little'))
                read_data = self.port.read(16)
                self.port.flushInput()
                self.rot_fan = int.from_bytes(read_data[0:2], byteorder='little')
                self.rot_turb = int.from_bytes(read_data[2:4], byteorder='little')
                self.current = int.from_bytes(read_data[4:6], byteorder='little', signed=True)
                self.voltage = int.from_bytes(read_data[6:8], byteorder='little', signed=True)
                self.thrust = int.from_bytes(read_data[8:11], byteorder='little', signed=True)
                self.anemometer = int.from_bytes(read_data[12:14], byteorder='little')
                self.potentiometer = int.from_bytes(read_data[14:16], byteorder='little')
                self.data_received = True
            else:
                warnings.warn('No data received. Transmit first.', TransmissionWarning)
        except:
            warnings.warn('serial connection lost during receiving', TransmissionWarning)
            self.port.close()
            self.arduino_connected = False
        self.__calculate_input()

    # Transmit data
    def write_to_arduino(self):
        try:
            if self.data_received:
                self.port.write(self.fan_pwm.to_bytes(1, byteorder='little'))
                self.port.write(self.servo_time.to_bytes(2, byteorder='little'))
                self.port.write(self.torque_level.to_bytes(1, byteorder='little', signed=True))
                self.port.write(self.led.to_bytes(1, byteorder='little'))
                self.port.flushOutput()
                self.data_received = False
            else:
                warnings.warn('No data transmitted. Receive first.', TransmissionWarning)
        except:
            warnings.warn('serial connection lost during transmitting', TransmissionWarning)
            self.port.close()
            self.arduino_connected = False

    # Input values
    def __calculate_input(self):
        self.dt = time.time() - self.time_last
        self.time_last = time.time()
        # Tip speed
        self.tip_speed = self.rot_turb / 60 * 2 * 3.14 * self.ROTOR_RADIUS
        self.v_rot = self.tip_speed

        # because current measurement is extremely noisy,
        # calculate current based on torque level and rotation speed
        if self.torque_level >= 0:
            self.torque = cal.DRIVETRAIN_FACTOR[self.torque_level] * self.rot_turb \
                          + cal.DRIVETRAIN_BIAS[self.torque_level]
        else:
            self.torque = 0
        # Power
        self.power_turb = 2 * 3.14 * self.rot_turb / 60 * self.torque
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
